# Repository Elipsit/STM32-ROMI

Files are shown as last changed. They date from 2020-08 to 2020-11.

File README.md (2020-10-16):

# STM32-ROMI

## Project Description

The Silicon Valley [HomeBrew Robotics Club](http://www.hbrobotics.org/) built an awesome [FPGA ROMI](https://github.com/hbrc-fpga-class) robot late 2019. I was inspired to build my own version using an STM32F4  while keeping the board compatable with the previous Polulu ROMI base. The purpose of this was to familiarize myself with the STM32 environment and get a cool robot out of it. 

The robot is designed to compete in the HBRC TableTop Challenge:

A challenge where robots succeed by staying on the table or paying the price.

Stage 1: Walk autonomously from one end of the table to the other without falling off.
Stage 2: Find and push a block off of the table.
Stage 3: Find and push a block off of the table into a box at the edge of the table.

### Project Status
Robot is operational - working on tuning the PID loop for smooth driving
 **This project is still a work in progress**

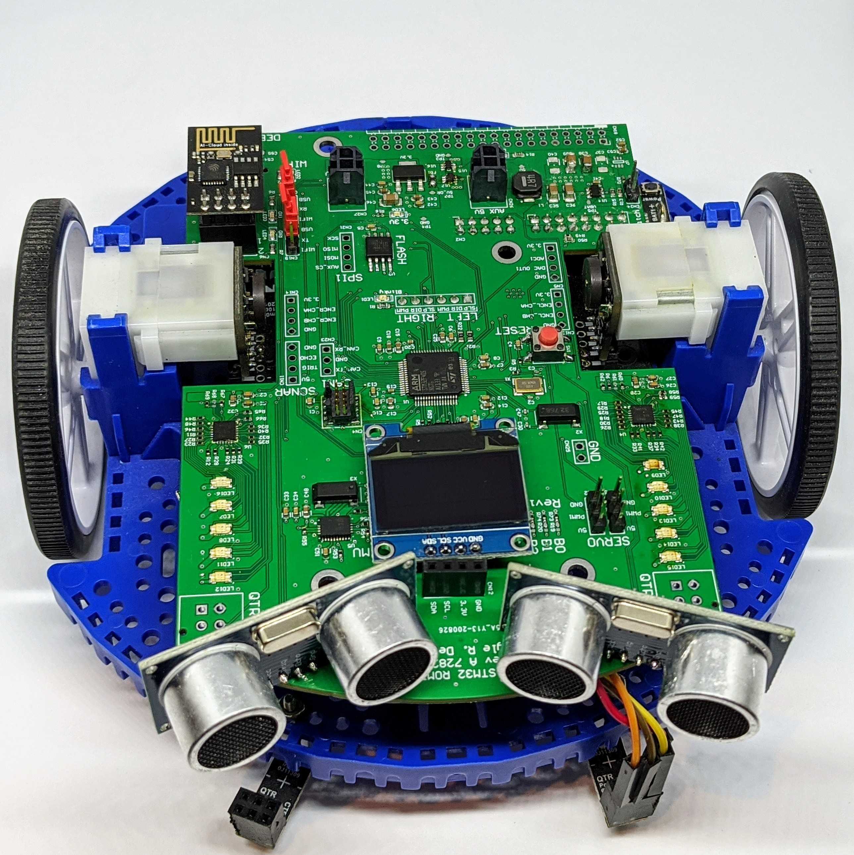
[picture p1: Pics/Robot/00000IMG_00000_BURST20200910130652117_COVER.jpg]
Robot_Front


## Design Files
### Electrical Design Files
This project was designed in Altium Designer 20

#### Datasheets
- [DRV8838 Motor Driver](https://www.ti.com/lit/ds/symlink/drv8838.pdf?HQS=TI-null-null-digikeymode-df-pf-null-wwe&ts=1599069814852)

### Motor Driver

The DRV8838 offers a simple two-pin PHASE/ENABLE control interface, which this board makes available for each motor as DIR and PWM, respectively. The DIR pin determines the motor direction (low drives the motor forward, high drives it in reverse) and the PWM pin can be supplied with a PWM signal to control the motor speed. The DIR and PWM control inputs are pulled low through weak internal pull-down resistors (approximately 100 kΩ). When the PWM pin is low, the motor outputs are both shorted to ground, which results in dynamic braking of a connected motor.

The two drivers’ SLEEP pins (labeled SLP) are connected together by default and can be driven low to put the drivers into a low-power sleep mode and turn off the motor outputs, which is useful if you want to let the motors coast. The SLEEP pins are pulled high through 10 kΩ pull-up resistors on the board so that the drivers are awake by default. In most applications, these pins can be left disconnected; if you want independent control of SLEEP on each side, you can cut the jumper labeled SLP L = R. The two SLEEP pins should not be driven separately without cutting this jumper.

The following simplified truth table shows how each driver operates:

#### Motor Driver Truth Table
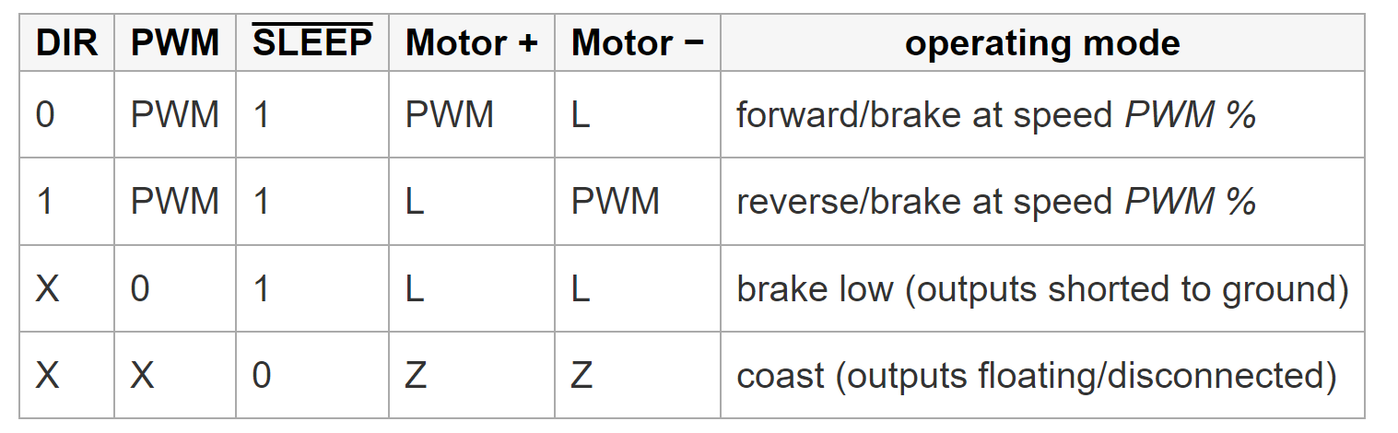
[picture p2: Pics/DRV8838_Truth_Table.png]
Truth Table


### PCBA
This project was manufactured by JLCPCB as an excuse for me to test their PCBA service.
*They didn't sponcer me I just wanted to try it out*

## Requited Parts

- [Romi Chassis Kit](https://www.pololu.com/product/3506)

- [Romi Encoder Pair Kit, 12 CPR, 3.5-18V](https://www.pololu.com/product/3542)

- [Motor Driver and Power Distribution Board for Romi Chassis](https://www.pololu.com/product/3543)

- [QTR-1A Reflectance Sensor (2-Pack)](https://www.pololu.com/product/2458)

- [0.96 Inch OLED](https://www.amazon.com/UCTRONICS-SSD1306-Self-Luminous-Display-Raspberry/dp/B072Q2X2LL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)

- [HC-SRO4](https://www.amazon.com/Smraza-Ultrasonic-Distance-Mounting-Duemilanove/dp/B01JG09DCK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)

### 3D Print Files
- [Sonar Servo Mount](https://www.thingiverse.com/thing:1423)

# Bring Up
The Uart2 channel can be connected to the CH340C; USB to serial converter, or an ESP8266 running [esp-link](https://github.com/jeelabs/esp-link) as a telnet connection

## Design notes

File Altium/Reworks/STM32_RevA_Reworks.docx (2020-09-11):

# STM32-ROMI Rev A Reworks

No table of contents entries found.

Date Modified | Revision | Author | Changes

# Wifi RX/TX

## Issue

Rx and Tx are flipped on ESP-01 moodule

## Solution

Cut trace and flywire

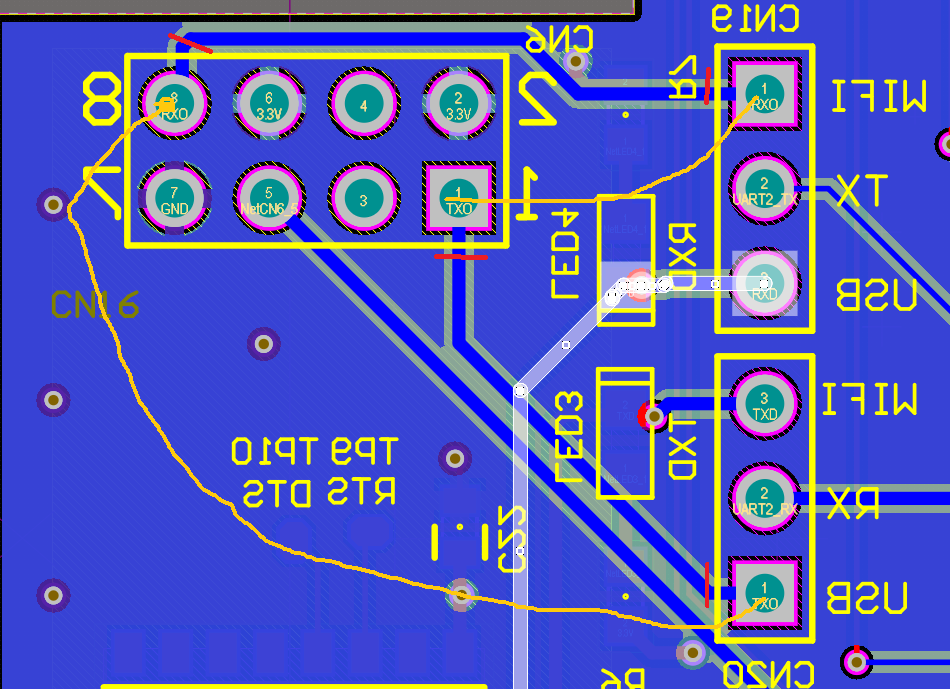
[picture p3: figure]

Cut the traces (cuts in red) at the base and fly wire correctly

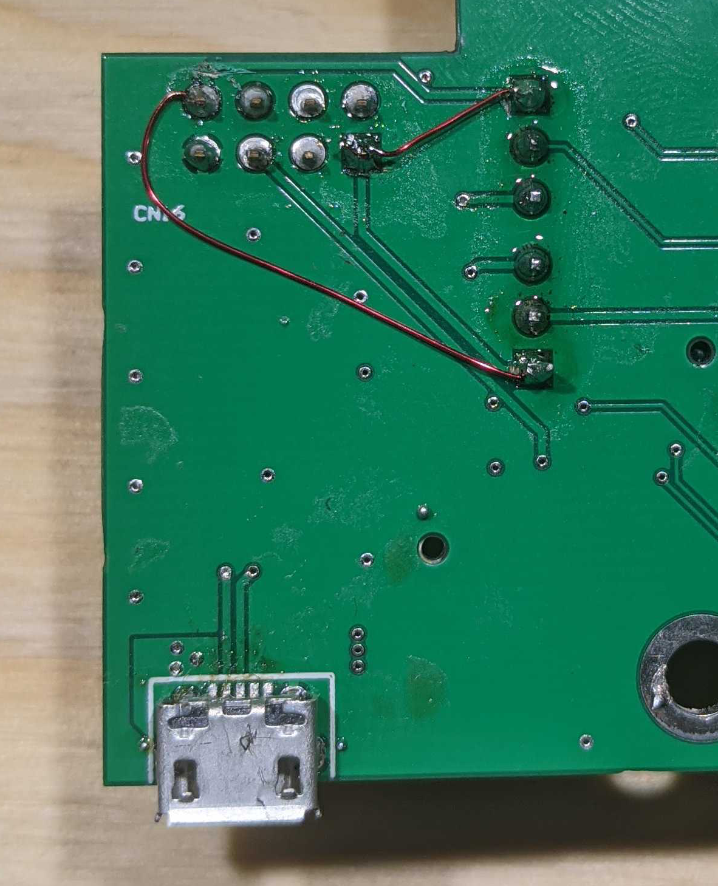
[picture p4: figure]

# PWMR

## Issue

Rx and Tx are flipped on ESP-01 moodule

## Solution

Cut trace and flywire

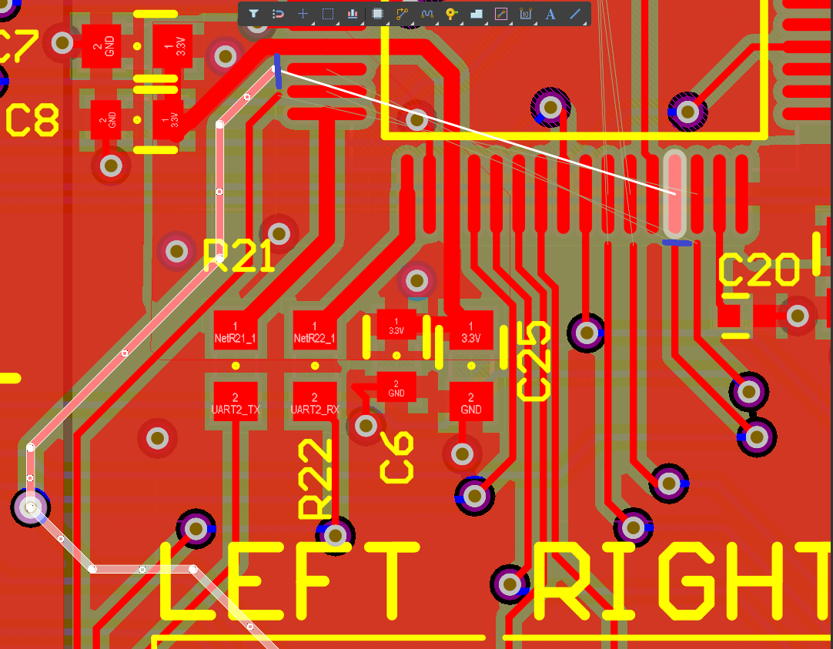
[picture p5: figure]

# PWMR

## Issue

Rx and Tx are flipped on ESP-01 moodule

## Solution

Cut trace and flywire

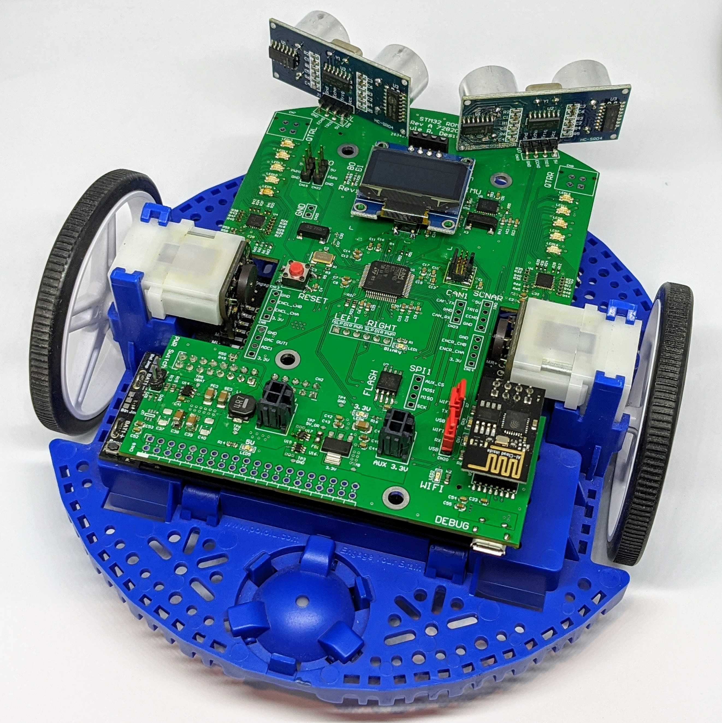
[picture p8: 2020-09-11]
Pics/Robot/00000IMG_00000_BURST20200910130628761_COVER.jpg

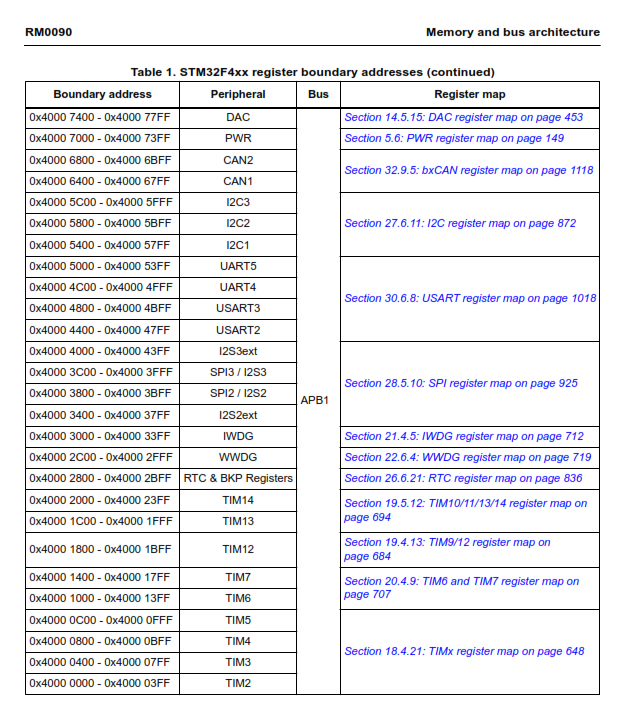
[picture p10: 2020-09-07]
Pics/Memory-2.png

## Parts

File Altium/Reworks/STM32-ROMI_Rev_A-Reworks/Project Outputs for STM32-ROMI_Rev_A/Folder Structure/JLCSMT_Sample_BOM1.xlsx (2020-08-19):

Comment | Designator | Footprint | LCSC Part #（optional）
100uF | C1 | CASE-B_3528 | C16133
100nF | C2, C9, C10 | 0603_C | C14663
10uF | C3-5 | 1206_C | C13585
15KΩ | R5, R6 | 0603_R | C22809

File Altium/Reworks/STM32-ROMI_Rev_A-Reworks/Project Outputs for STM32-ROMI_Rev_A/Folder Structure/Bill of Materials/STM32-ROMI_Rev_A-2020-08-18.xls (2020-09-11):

Item # | Designator | Description | Name | Quantity | Manufacturer 1 | Manufacturer Part Number 1 | Footprint | LibRef | Note
1 | R4, R51, R52, R64, R69, R71, R73, R74, R75 | 0.0 0402 | 0 | 9 | Panasonic | ERJ-2GE0R00X | RESC0402(1005)_L | RES 0.0 OHM JUMPER 1/10W 0402
2 | R21, R22 | 0 0603 | 0 0603 | 2 | Vishay Dale | CRCW06030000Z0EAHP | RESC0603(1608)_N | RES 0.0 OHM 1/4W JUMP 0603 SMD
3 | C6, C26, C29, C33 | 0.01uF 50V 0603 | 0.01uF | 4 | KEMET | C0603C103K5RACTU | CAPC0603(1608)_L | CAP CER 0.01uF 50V 10% X7R 0603
4 | C1, C4, C5, C8, C9, C10, C11, C12, C13, C24, C27, C31, C34, C51 | 0.1uF 0603 16V | 0.1uF | 14 | KEMET | C0603C104K4RACTU | CAPC0603(1608)_L | CAP CER 0.1UF 16V 10% X7R 0603
5 | C21, C22, C23, C41, C42, C44, C52, C54 | 0.1uF 0603 16V | 0.1uF | 8 | KEMET | C0603C104K4RACTU | CAPC0603(1608)_L | CAP CER 0.1UF 16V 10% X7R 0603
6 | R27, R28, R29, R30, R39, R40, R41, R42, R47, R48 | 1K 0402 | 1K | 10 | Mepco Philips | RC0402FR-071KL | RESC0402(1005)_L | RES 1K OHM 1% 1/16W 0402
7 | R2, R6, R7, R14 | 1.0K 0603 | 1.0K | 4 | Stackpole Electronics | RMCF0603FT1K00 | RESC0603(1608)_N | RES 1K OHM 1% 1/10W 0603
8 | C7, C14, C15, C16, C17, C25, C28, C32, C43, C45, C48, C53, C55 | 1uF 0603 25V | 1uF | 13 | TDK | CGA3E1X7R1E105K080AC | CAPC0603(1608)_N | CAP CER 1UF 25V 10% X7R 0603
9 | C19, C20 | 2.2uF 0402 | 2.2uF | 2 | TDK | C1005X5R1V225K050BC | CAPC0402(1005)_L | CAP CER 2.2UF 35V 10% X5R 0402
10 | L1 | Power Inductors 3.3uH ±20% 5.5A SMD,5.2x4.7x3mm RoHS | 3.3uH 5.5A | 1 |  |  | YSPI0530-3R3M | FIXED IND 3.3UH 5.5A 28 MOHM SMD
11 | U16 | 3.3 volt fixed regulator, 800mA | 3.3V | 1 | STMicroelectronics | LD1117S33TR | DSO-G3 | LD1117S33
12 | LED6 | LED GREEN CLEAR THIN 0603 SMD | 3.3V | 1 | Vishay Lite-On | LTST-C191KGKT | SM-LED-0603 | LTST-C191KGKT
13 | R56, R57, R58, R59, R60, R65, R66, R67 | 4.7K 0402 | 4.7K | 8 | Yageo | RC0402FR-074K7L | RESC0402(1005)_N | RES 4.7K OHM 1% 1/10W 0402
14 | LED5 | LED GREEN CLEAR THIN 0603 SMD | 5V | 1 | Vishay Lite-On | LTST-C191KGKT | SM-LED-0603 | LTST-C191KGKT
15 | X1 | 8Mhz ABM3 Parallel Load Crystal | 8Mhz | 1 | Abracon | ABM3B-8.000MHZ-B2-T | SMXOSC/5x3.2 | CRYSTAL 8MHZ ABM3
16 | R53, R54, R55, R62 | 10K 0402 | 10K | 4 | Samsung | RC1005F103CS | RESC0402(1005)_N | RES 10K OHM 1% 1/16W 0402
17 | R8, R9, R10, R15, R50 | 10K 0603 | 10K 1% | 5 | Panasonic | ERJ-3EKF1002V | RESC0603(1608)_L | RES 10K OHM 1/10W 1% 0603 SMD
18 | C35, C36, C37, C38, C39, C40, C46 |  | 10uF | 7 | Murata | GCM31CR71C106KA64L | CAPC1206(3216)_M | CAP CER 10UF 16V 1206
19 | C18 | 10uF 0603 10V | 10uF | 1 | Taiyo Yuden | LMK107BBJ106MAHT | CAPC0603(1608)_L | CAP CER 10UF 10V 20% X5R 0603
20 | C2, C3, C30, C47, C49, C50 | 20pF 0402 | 20pF 0402 | 6 | Murata | GRM1555C1H200GA01D | CAPC0402(1005)_L | CAP CER 20PF 50V 2% NP0 0402
21 | X2, X3 | SMD CRYSTAL RESONATORS 32.768KHZ ±20PPM SMD-3215_2P ROHS | 32.768 XO | 2 | Abracon | ABS25-32.768KHZ-6-T | OSCABS | DST310S 32.768KHz
22 | R13 | RES SMD 56.2K OHM 1% 1/10W 0603 | 56.2K | 1 | Panasonic | ERJ-3EKF5622V | RESC0603(1608)_L | RES SMD 56.2K OHM 1% 1/10W 0603
23 | R16 | 100 0402 | 100 | 1 | Yageo | RC0402FR-07100RL | RESC0402(1005)_N | RES 100 OHM 1% 1/16W 0402
24 | R5, R49, R70 | 100K 0402 | 100K 0402 | 3 | SEI | RMCF0402FT100K | RESC0402(1005)_L | RES 100K OHM 1% 1/16W 0402
25 | R3 | 220 0402 | 220 | 1 | Panasonic | ERJ-2RKF2200X | RESC0402(1005)_L | RES 220 OHM 1% 1/10W 0402
26 | R1 | 576OHMS ±1% 1/10W 0603 | 576 | 1 |  |  | RESC0603(1608)_N | 576
27 | FB1 | 600 OHM 0805 2.0A | 600 Ohm @ 100MHz | 1 | Wurth Electronics | 742792040 | RESC0805(2012)_N | FERRITE 600 OHM 2.0A 0805
28 | R11, R12, R17, R18, R23, R24, R25, R26, R31, R32, R33, R34, R35, R36, R37, R38, R43, R44, R45, R46 | 604 0402 | 604 | 20 | Panasonic | ERA-2AEB6040X | RESC0402(1005)_L | RES 604 OHM 1% 1/10W 0402
29 | CN27 | Molex Microfit 1x2 Vert Header | AUX 3.3V | 1 | Molex | 430450227 | Molex 1x2 Microfit 3.0 | MICROFIT 3.0 HDR VERT CPI 2CKT
30 | CN26 | Molex Microfit 1x2 Vert Header | AUX 5V | 1 | Molex | 430450227 | Molex 1x2 Microfit 3.0 | MICROFIT 3.0 HDR VERT CPI 2CKT
31 | LED1 | LED GREEN CLEAR THIN 0603 SMD | Blinky | 1 | Vishay Lite-On | LTST-C191KGKT | SM-LED-0603 | LTST-C191KGKT
32 | U5 | 9-Axis Intertial Sensor | BNO055 | 1 |  |  | LGA-28-3.8x5.2mm | CMP-010-0024-02
33 | CN23 | Header, 3-Pin | CAN1 | 1 | Sullins | PRPC003SAAN-RC | HDR1X3 | Header 3
34 | U3 | USB to Serial UART | CH340C | 1 |  |  | SOP-16 | CH340C
35 | CN6 | Header, 4-Pin, Dual row | CN/ESP-01 | 1 |  |  | ESP-01 | CN/ESP-01
36 | LED7, LED8, LED9, LED10, LED11, LED12, LED13, LED14, LED15, LED16 | RGB 620NMRED, 520NMGREEN, 465NMBLUE SMD, | E6C1206RGBC3UDA | 10 |  |  | E6C1206RGBC3UDA | RGB LED
37 | CN25 | Header, 2-Pin | GND | 1 | Sullins | PRPC002SAAN-RC | HDR1X2 | Header 2
38 | CN15, CN22 | Header, 3-Pin | Header 3 | 2 | Sullins | PRPC003SAAN-RC | HDR1X3 | Header 3
39 | CN5, CN9, CN10, CN11, CN12, CN13, CN14, CN21 | Header, 4-Pin | Header 4 | 8 | Sullins | PRPC004SAAN-RC | HDR1X4 | Header 4
40 | CN1 | Header, 6-Pin | Header 6 | 1 | Sullins | PRPC006SAAN-RC | PinHeader_1x06_P2.54mm_Vertical | Romi_Header 6
41 | CN18 | Header, 20-Pin, Dual row | Header 20X2 | 1 | Harwin | M20-9762046 | Raspberry_Pi_2_3 | J/Header 20X2
42 | U7, U15, U17 | OR Controller P-Channel 1.5A CC | Ideal Diode | 3 | Texas Instruments | LM66100DCKT | SC-70-6 | LM66100DCKT
43 | CN4 | SAMTEC - FTSH-105-01-L-DV - HEADER, 1.27MM, SMD, 10WAY | JTAG | 1 | Samtec | FTSH-105-01-L-DV | BOBS FAVORITE DEBUG HDR | CONN-2x5-SWD
44 | CN16 | Amphenol FCI CONN USB MICRO B RECPT SMT R/A | MicroUSB | 1 | Amphenol ICC / FCI | 10118194-0001LF | 10118194-0001LF | 10118194-0001LF
45 | U2 | 16M NOR Flash | MX25L1606E | 1 | Macronix | MX25L1606EM2I-12G | SOG.050/8D | MX25L1606E
46 | CN17 | SSD1306 I2C OLED 0.96" | OLED 0.96" | 1 |  |  | OLED_0.96_I2C | OLED_0.96_I2C
47 | CN24 | Header, 2-Pin | PWR Switch | 1 | Sullins | PRPC002SAAN-RC | HDR1X2 | Header 2
48 | CN7 | Molex Microfit 2x2 Vert Header | QTR_LEFT | 1 | Molex | 430450427 | Molex 2x2 Microfit | MICROFIT 3.0 HDR VERT 4CKT
49 | CN8 | Molex Microfit 2x2 Vert Header | QTR_RIGHT | 1 | Molex | 430450427 | Molex 2x2 Microfit | MICROFIT 3.0 HDR VERT 4CKT
50 | SW1, SW2 | SWITCH TACTILE SPST-NO 0.05A 12V | RESET | 2 | ITT C&K | PTS645SK50SMTR92LFS | SW TACT Red 6mm x 6mm | SW-PB SMD 5mm Red
51 | CN3 | Header, 8-Pin, Dual row | Romi_Header 8X2 | 1 |  |  | PinHeader_2x08_P2.54mm_Vertical | Romi_Header 8X2
52 | CN2 | Header, 5-Pin, Dual row | Romi-Header 5X2 | 1 |  |  | PinHeader_2x05_P2.54mm_Vertical - duplicate | Romi-Header 5X2
53 | LED4 | LED GREEN CLEAR THIN 0603 SMD | RXD | 1 | Vishay Lite-On | LTST-C191KGKT | SM-LED-0603 | LTST-C191KGKT
54 | U1 | IC MCU 32BIT 1MB FLASH 64LQFP | STM32F405RGT6 | 1 | STMicroelectronics | STM32F405RGT6 | STM-LQFP64_N | STM32F405RGT6
55 | CN20 | Header, 3-Pin | STM_RX | 1 | Sullins | PRPC003SAAN-RC | HDR1X3 | Header 3
56 | CN19 | Header, 3-Pin | STM_TX | 1 | Sullins | PRPC003SAAN-RC | HDR1X3 | Header 3
57 | U4, U6 | IC I/O EXPANDER I2C SMBUS 24VQFN | TCA9555RGER | 2 | Texas Instruments | TCA9555RGER | QFN50P400X400X100_HS-25N | CMP-001-0784-04
58 | U14 | IC REG BUCK ADJ 3A TSOT23-6 | TPS563209DDCR | 1 | Texas Instruments | TPS563209DDCR | SOT23-6 | TPS563209DDCR
59 | LED3 | LED GREEN CLEAR THIN 0603 SMD | TXD | 1 | Vishay Lite-On | LTST-C191KGKT | SM-LED-0603 | LTST-C191KGKT
60 | LED2 | LED GREEN CLEAR THIN 0603 SMD | WIFI | 1 | Vishay Lite-On | LTST-C191KGKT | SM-LED-0603 | LTST-C191KGKT

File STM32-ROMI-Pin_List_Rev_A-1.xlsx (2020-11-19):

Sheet: Pin Map
Chip Line: | STM32F405RGT6 |  |  |  |  | STM32F405RGT6 | OLD
Pin Number | Pin Name | Net Class | Net Name | Connected Component | Old Pin | Pin Name | Net Class | Net Name | Connected Component
60 | BOOT0 |  |  |  |  | BOOT0
7 | NRST | Reset |  |  |  | NRST | Reset
14 | PA0 | Encoder | ENCL_CHA |  | PB10 | PA0 | PWM | PWMR | CN1
15 | PA1 | Encoder | ENCL_CHB |  | PB11 | PA1 | ADC | ADC_IN1
43 | PA10 | SONAR | TRIGR |  |  | PA10 | SONAR | TRIGR
44 | PA11 | CAN | CAN_RX |  |  | PA11 | CAN | CAN_RX
45 | PA12 | CAN | CAN_TX |  |  | PA12 | CAN | CAN_TX
46 | PA13 | SWO | SWDIO | PROGRAMMER |  | PA13 | SWO | SWDIO | PROGRAMMER
49 | PA14 | TCK | SWCLK | PROGRAMMER |  | PA14 | TCK | SWCLK | PROGRAMMER
50 | PA15 | SPI | SPI_CS_AUX |  |  | PA15 | SPI | SPI_CS_AUX
16 | PA2 | UART | UART2_TX |  |  | PA2 | UART | UART2_TX
17 | PA3 | UART | UART2_RX |  |  | PA3 | UART | UART2_RX
20 | PA4 | DAC | DAC_OUT1 |  |  | PA4 | DAC | DAC_OUT1
21 | PA5 | GPIO | BLINKY | LEDx |  | PA5 | GPIO | BLINKY | LEDx
22 | PA6 | SPI1 | SPI1_MISO |  |  | PA6 | SPI1 | SPI1_MISO
23 | PA7 | SPI1 | SPI1_MOSI |  |  | PA7 | SPI1 | SPI1_MOSI
41 | PA8 | I2C3 | I2C3_SCL |  |  | PA8 | I2C3 | I2C3_SCL
42 | PA9 | SONAR | ECHOR |  |  | PA9 | SONAR | ECHOR
26 | PB0 | SONAR | TRIGL |  |  | PB0 | Encoder | ENCR_CHA | CN14
27 | PB1 | SONAR | ECHOL |  |  | PB1 | Encoder | ENCR_CHB | CN15
29 | PB10 | PWM | PWMR | CN1 |  | PB10 | Encoder | ENCL_CHA | CN13
30 | PB11 | ADC |  |  |  | PB11 | Encoder | ENCL_CHB | CN14
33 | PB12 | QTR | QTRL_OUT |  |  | PB12 | QTR | QTRL_OUT
34 | PB13 | Motor CTRL | ROMI_DIRR |  |  | PB13 | Motor CTRL | ROMI_DIRR
35 | PB14 | Motor CTRL | ROMI_SLPR |  |  | PB14 | Motor CTRL | ROMI_SLPR
36 | PB15 | Servo | SERVO1_PWM |  |  | PB15 | Servo | SERVO1_PWM
28 | PB2 | QTR | QTRR_OUT |  |  | PB2 | QTR | QTRR_OUT
55 | PB3 | SPI1_SCK | SPI1_SCK |  |  | PB3 | SPI1_SCK | SPI1_SCK
56 | PB4 | Encoder | ENCR_CHA |  |  | PB4 | SONAR | TRIGL
57 | PB5 | Encoder | ENCR_CHB |  |  | PB5 | SONAR | ECHOL
58 | PB6 | PWM | ROMI_PWML | CN1 |  | PB6 | PWM | ROMI_PWML | CN1
59 | PB7 | I2C | I2C1_SDA |  |  | PB7 | I2C | I2C1_SDA
61 | PB8 | I2C | I2C1_SCL |  |  | PB8 | I2C | I2C1_SCL
62 | PB9 | Servo | SERVO2_PWM |  |  | PB9 | Servo | SERVO2_PWM
8 | PC0 | IMU | IMU_RST |  |  | PC0 | IMU | IMU_RST
9 | PC1 | Revision Bits | REV_BIT0 |  |  | PC1 | Revision Bits | REV_BIT0
51 | PC10 | UART RPI | UART4_TX |  |  | PC10 | UART RPI | UART4_TX
52 | PC11 | UART RPI | UART4_RX |  |  | PC11 | UART RPI | UART4_RX
53 | PC12 | Motor CTRL | ROMI_DIRL |  |  | PC12 | Motor CTRL | ROMI_DIRL
2 | PC13 | GPIO | OLED_BTN | Push Button |  | PC13 | GPIO | OLED_BTN | Push Button
3 | PC14 | RCC | RCC_OSC32_IN |  |  | PC14 | RCC | RCC_OSC32_IN
4 | PC15 | RCC | RCC_OSC32_OUT |  |  | PC15 | RCC | RCC_OSC32_OUT
10 | PC2 | Revision Bits | REV_BIT1 |  |  | PC2 | Revision Bits | REV_BIT1
11 | PC3 | Revision Bits | REV_BIT2 |  |  | PC3 | Revision Bits | REV_BIT2
24 | PC4 | RGB | RGB_INT1 |  |  | PC4 | RGB | RGB_INT1
25 | PC5 | RGB | RGB_INT2 |  |  | PC5 | RGB | RGB_INT2
37 | PC6 | Motor CTRL | ROMI_SLPL |  |  | PC6 | Motor CTRL | ROMI_SLPL
38 | PC7 | SONAR | ECHO_CTR |  |  | PC7 | SONAR | ECHO_CTR
39 | PC8 | SONAR | TRIG_CTR |  |  | PC8 | SONAR | TRIG_CTR
40 | PC9 | I2C3 | I2C3_SDA |  |  | PC9 | I2C3 | I2C3_SDA
54 | PD2 | Flash CS | SPI_CS_FLASH |  |  | PD2 | Flash CS | SPI_CS_FLASH
5 | RCC_OSC_IN | RCC | RCC_OSC_IN |  |  | RCC_OSC_IN | RCC | RCC_OSC_IN
6 | RCC_OSC_OUT | RCC | RCC_OSC_OUT |  |  | RCC_OSC_OUT | RCC | RCC_OSC_OUT
1 | VBAT | 3.3V | VBAT | 3.3V |  | VBAT | 3.3V | VBAT | 3.3V
13 | VDD |  |  |  |  | VDD
19 | VDD |  |  |  |  | VDD
32 | VDD |  |  |  |  | VDD
48 | VDD | Power |  |  |  | VDD | Power
64 | VDD |  |  |  |  | VDD
12 | VSS |  |  |  |  | VSS
18 | VSS |  |  |  |  | VSS
31 | VSS |  |  |  |  | VSS
47 | VSS | GND |  |  |  | VSS | GND
63 | VSS |  |  |  |  | VSS

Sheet: Timer Map
 |  |  |  |  | OLD
Type | Name | Purpose | Net |  | Type | Name | Purpose | Net
RTC | RTC |  |  |  | RTC | RTC
Advanced-Control Timer | TIM1 |  |  |  | Advanced-Control Timer | TIM1
General Purpose Timer | TIM2 | PWM Motor | PWM Right |  | General Purpose Timer | TIM2 | Encoder | Encoder Left
General Purpose Timer | TIM3 | Encoder | Encoder Right |  | General Purpose Timer | TIM3 | Encoder | Encoder Right
General Purpose Timer | TIM4 | PWM Motor | PWM Left |  | General Purpose Timer | TIM4 | PWM Motor | PWM Left
General Purpose Timer | TIM5 | Encoder | Encoder Left |  | General Purpose Timer | TIM5 | PWM Motor | PWM Right
Basic Timer | TIM6 | Blinky |  |  | Basic Timer | TIM6 | Blinky
Basic Timer | TIM7 | Encoder Poll |  |  | Basic Timer | TIM7 | Encoder Poll
Advanced-Control Timer | TIM8 |  |  | Change to use for gpio interupt. Reset timer, send trigger and increment timer to count. | Advanced-Control Timer | TIM8
General Purpose Timer | TIM9 | Ultrasonic mSec |  |  | General Purpose Timer | TIM9 | Ultrasonic mSec
General Purpose Timer | TIM10 |  |  |  | General Purpose Timer | TIM10
General Purpose Timer | TIM11 | Servo | Servo2 PWM |  | General Purpose Timer | TIM11 | Servo | Servo2 PWM
General Purpose Timer | TIM12 | Servo | Servo1 PWM |  | General Purpose Timer | TIM12 | Servo | Servo1 PWM
General Purpose Timer | TIM13 |  |  |  | General Purpose Timer | TIM13
General Purpose Timer | TIM14 |  |  |  | General Purpose Timer | TIM14

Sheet: Math
Sample Rate | 50 | HZ
Sample Period | 0.02 | Sec
Encoder Resolution | 12
Gear Ratio | 100 | to 1
Counts/rev | 1200
Wheel Diameter | 72 | mm
Wheel Circumference | 226.188 | mm
Counts/mm | 5.305321237
MAX RPM | 130 | rpm
Max RPS | 2.166666667 | rps
Max Rad/s | 13.60666667
Max Counts/Sec | 2600
Max Counts per sample | 52 | 1/sec
Counts/rad | 190.9915645
Enc to Rad/s | 0.2616666667
Enc/Vel
Rad/s

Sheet: Timer Calculator
Timer 2 | Motor Left
APB1 Timer Clock | Prescaler | Period | Frequency (HZ) | Interupt (Sec)
50000000 | 3 | 999 | 16683.35002 | 5.994e-05
Timer 4 | Motor Right
APB1 Timer Clock | Prescaler | Period | Frequency (HZ) | Interupt (Sec)
50000000 | 2 | 1000 | 25000 | 4e-05

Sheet: ROMI Connectors
Name | X | Y | Rotation | Layer
CN1 | 1939.5mil | 1879mil | 90 | Bottom
CN2 | 1939.5mil | 1086.1mil | 0 | Top
CN3 | 1339.5mil | 1086.1mil | 270 | Bottom

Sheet: Libraries
Neopixel | https://github.com/hubmartin/WS2812B_STM32F4
Possible LED Driver | https://lcsc.com/product-detail/LED-Drivers_MBI5020GP_C82600.html
clone of this | https://lcsc.com/product-detail/_STMicroelectronics_STP16CPC26MTR_STP16CPC26MTR_C157439.html
possible speaker | https://lcsc.com/product-detail/Audio-Power-OpAmps_AWINIC-Shanghai-Awinic-Tech-AW8736FCR_C252442.html

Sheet: I2C Map
Address | Component

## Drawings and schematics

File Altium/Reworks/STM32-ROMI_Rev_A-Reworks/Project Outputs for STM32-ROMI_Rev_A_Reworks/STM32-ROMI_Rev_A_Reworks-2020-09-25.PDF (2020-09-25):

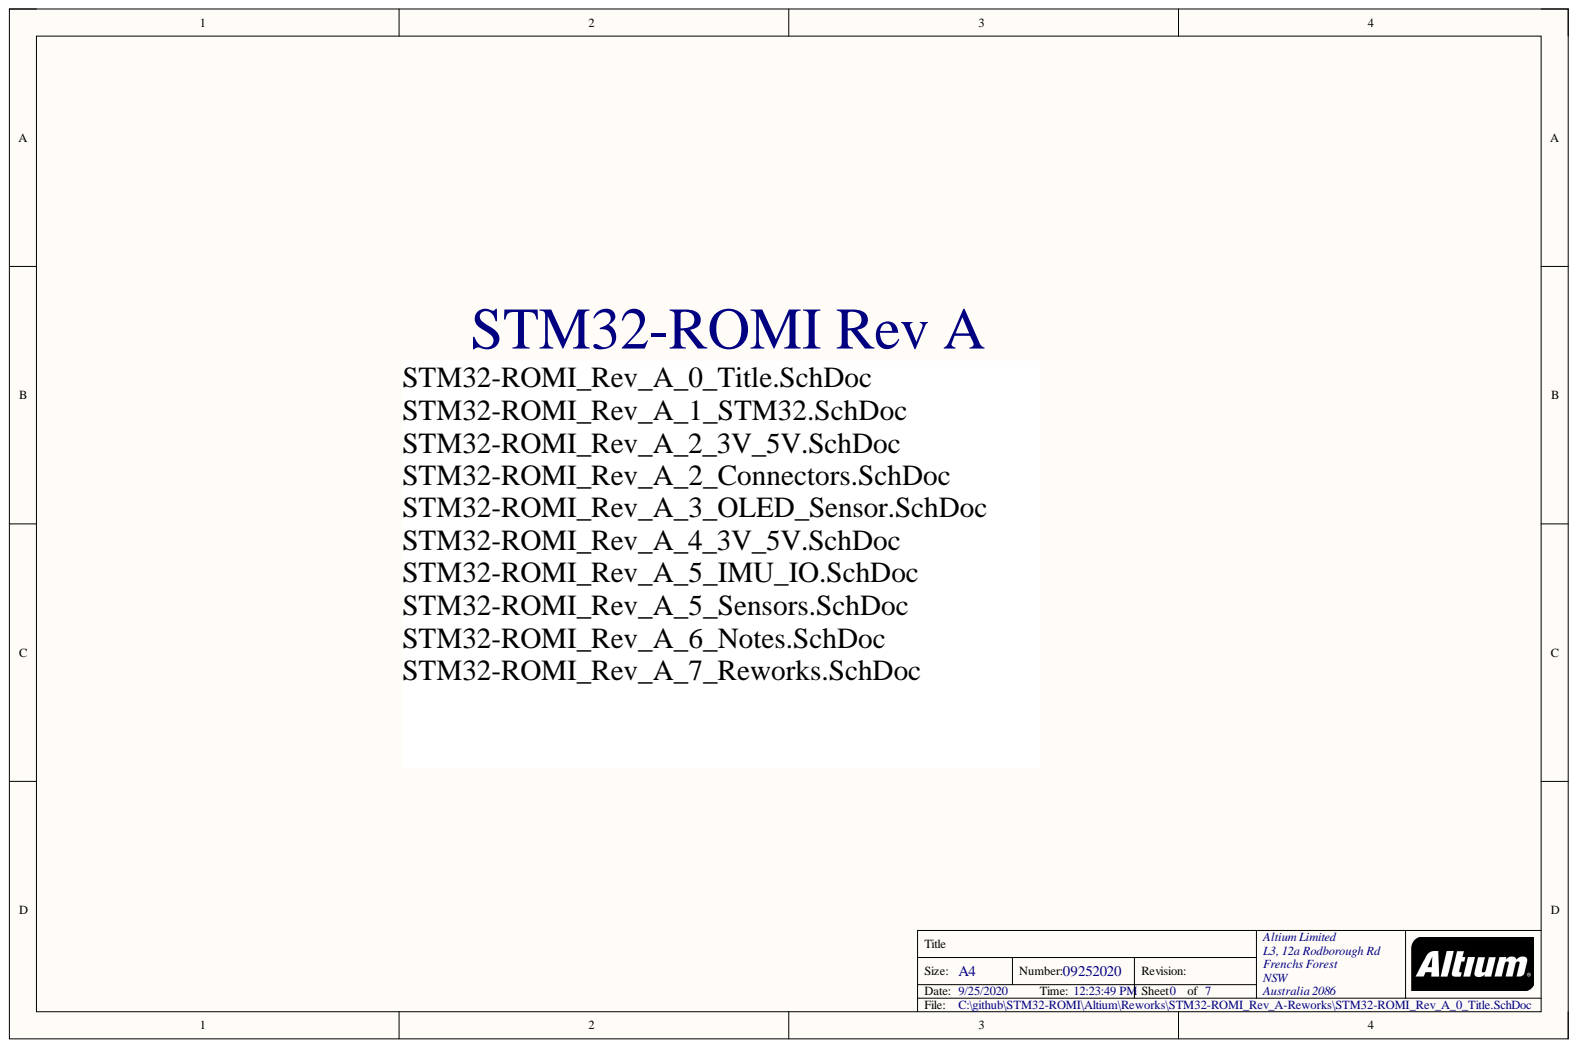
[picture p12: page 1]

Title | Altium Limited L3, 12a Rodborough Rd Frenchs Forest NSW Australia 2086

A4 Size: | 09252020 Number: | Revision:

Date: 9/25/2020 Time: 12:23:49 PM | | Sheet 0 of 7

C:\github\STM32-ROMI\Altium\Reworks\STM32-ROMI_Rev_A-Reworks\STM32-ROMI_Rev_A_0_Title.SchDoc

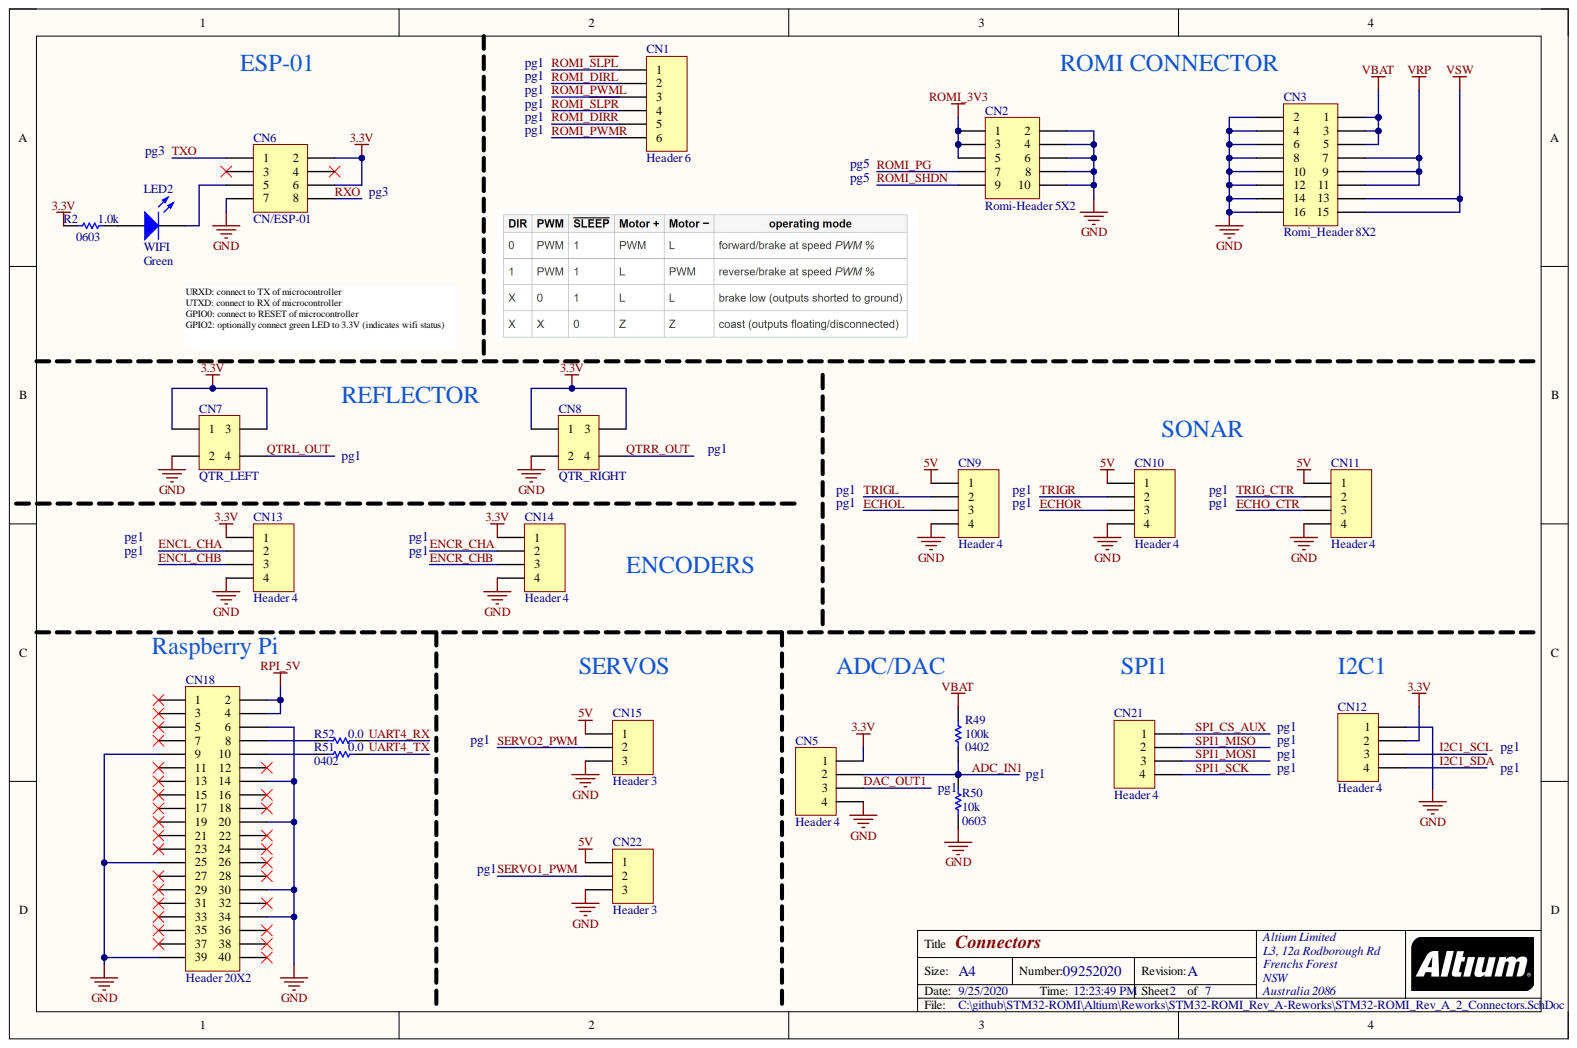
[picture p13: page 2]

URXD: connect to TX of microcontroller
UTXD: connect to RX of microcontroller
GPIO0: connect to RESET of microcontroller
GPIO2: optionally connect green LED to 3.3V (indicates wifi status)

Connectors Title | Altium Limited L3, 12a Rodborough Rd Frenchs Forest NSW Australia 2086

A4 Size: | 09252020 Number: | A Revision:

Date: 9/25/2020 Time: 12:23:49 PM | | Sheet 2 of 7

C:\github\STM32-ROMI\Altium\Reworks\STM32-ROMI_Rev_A-Reworks\STM32-ROMI_Rev_A_2_Connectors.SchDoc

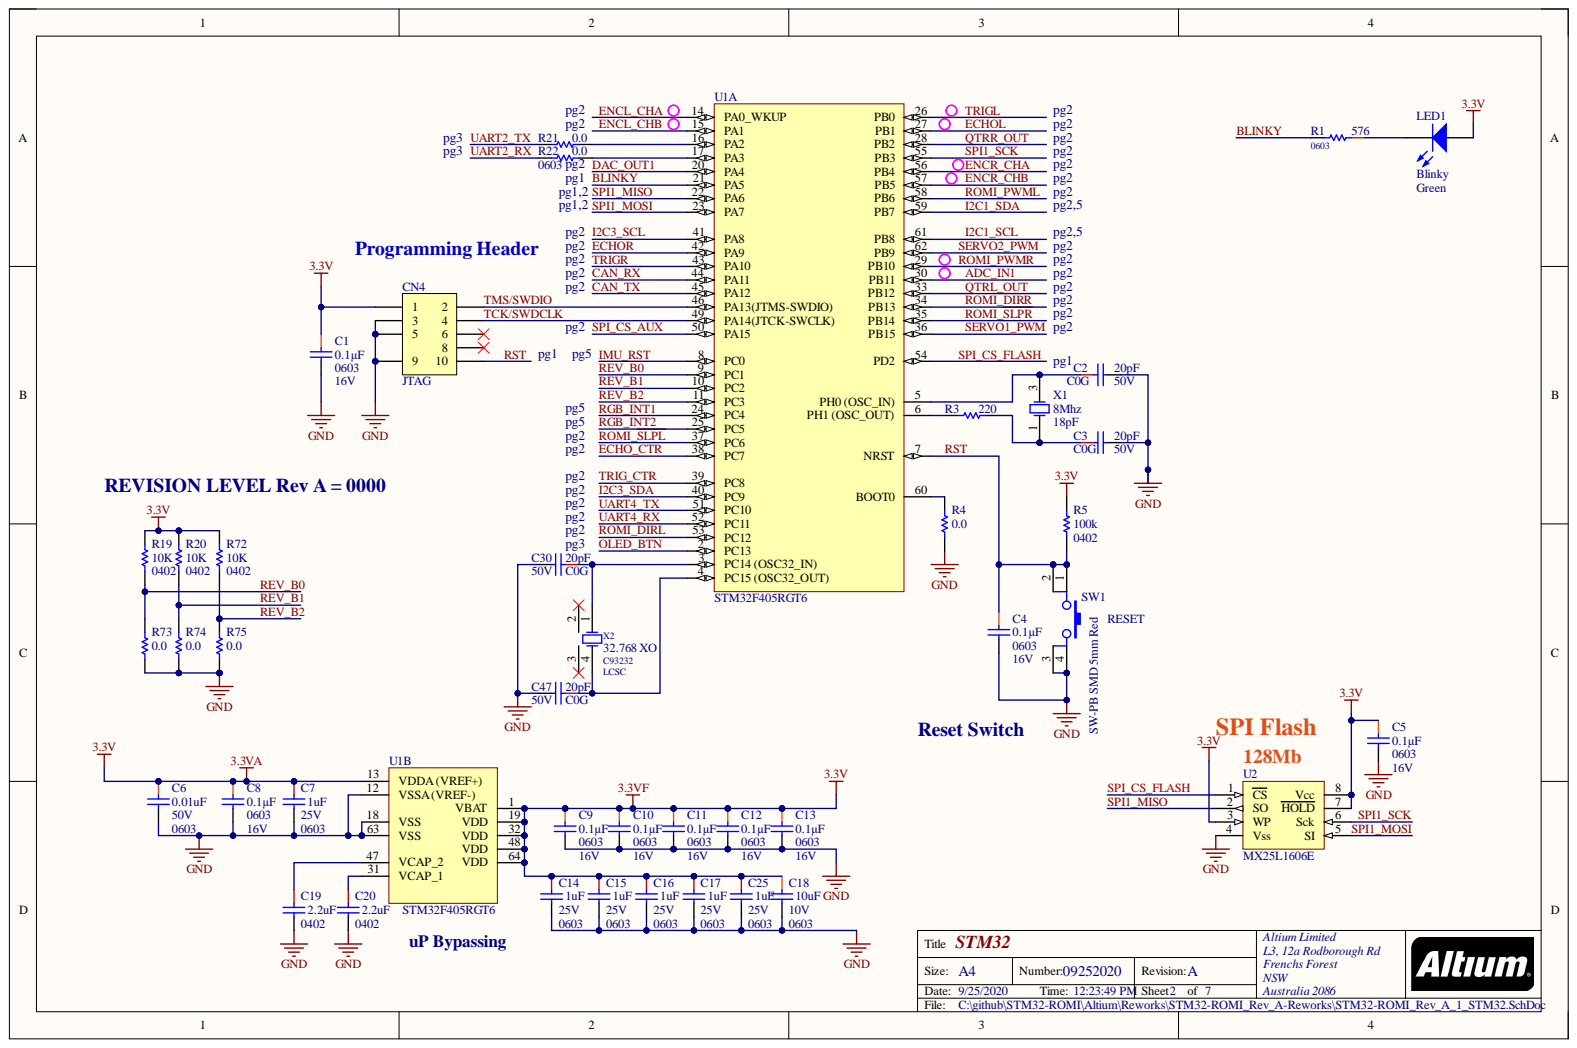
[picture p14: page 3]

TCK/SWDCLK | PA14(JTCK-SWCLK) 49 | ROMI_SLPR

SPI_CS_AUX pg5 pg2 pg2 pg2 pg2 pg2 | PA15 50 | SERVO1_PWM

0.0 | | REV_B1

0.0 | REV_B2

C:\github\STM32-ROMI\Altium\Reworks\STM32-ROMI_Rev_A-Reworks\STM32-ROMI_Rev_A_1_STM32.SchDoc

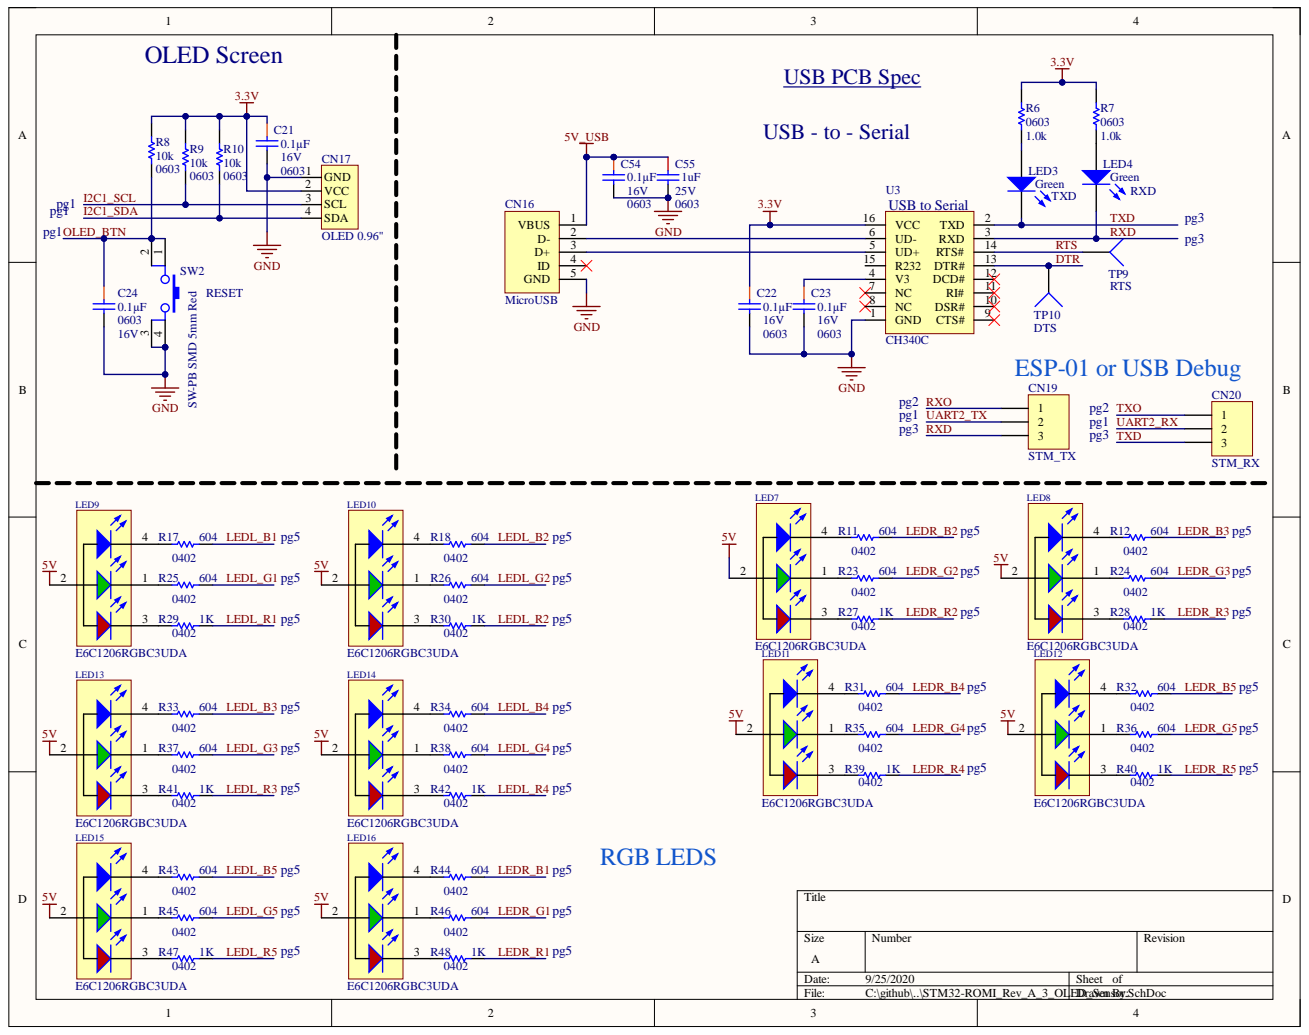
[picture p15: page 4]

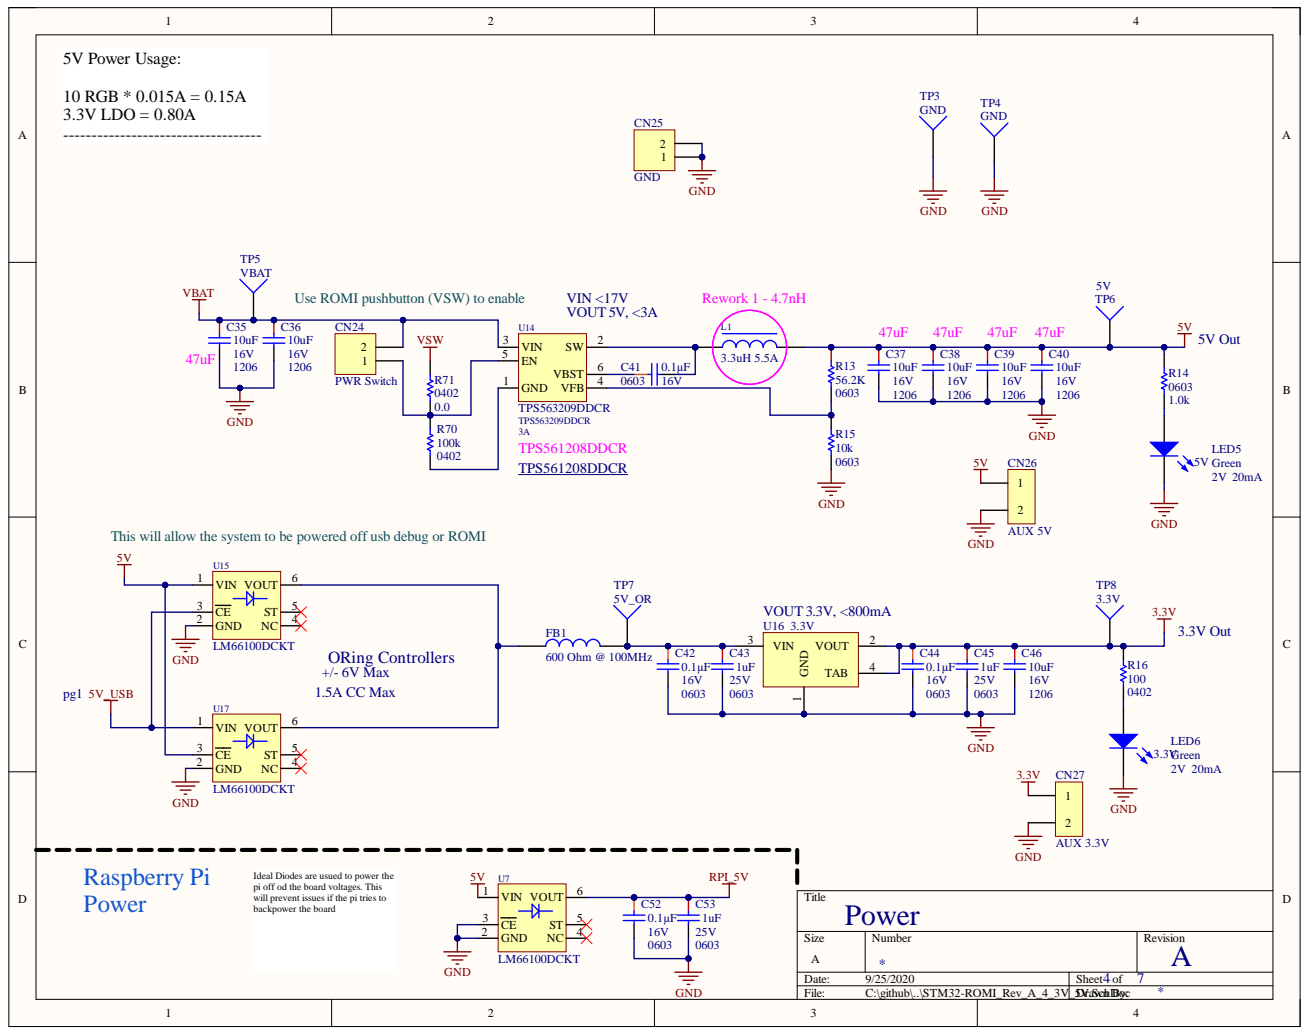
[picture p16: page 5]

Use ROMI pushbutton (VSW) to enable

This will allow the system to be powered off usb debug or ROMI

Ideal Diodes are usued to power the
pi off od the board voltages. This
will prevent issues if the pi tries to
backpower the board

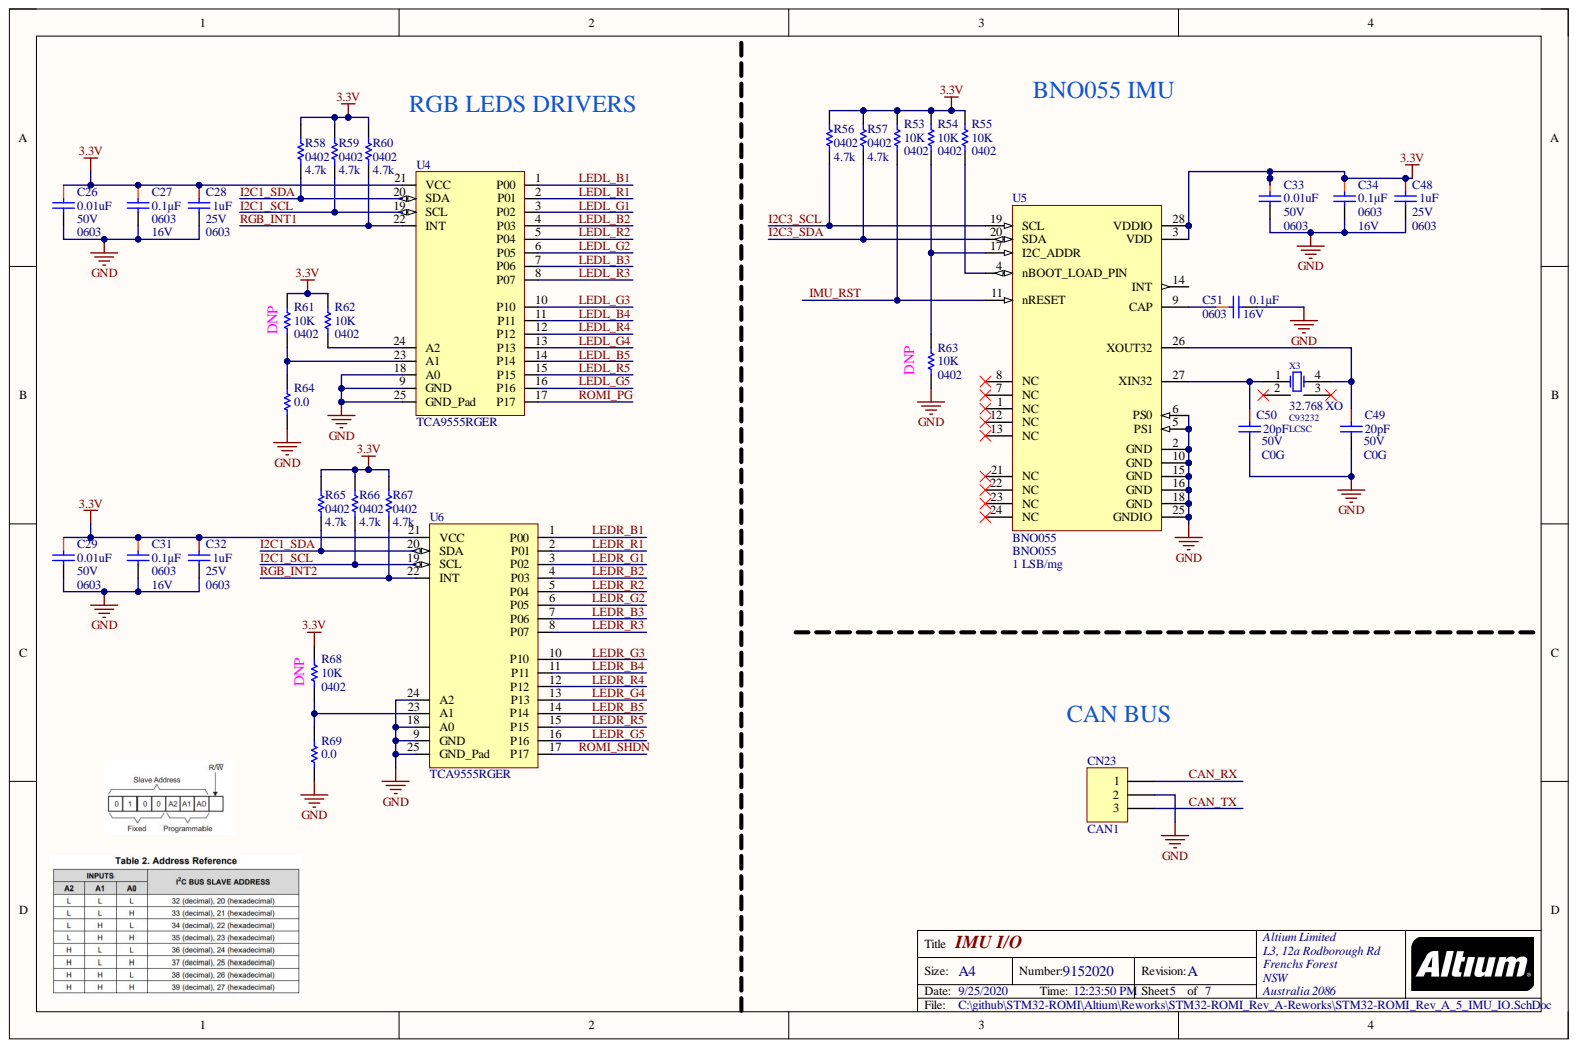
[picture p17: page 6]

IMU I/O Titl e | Altium L i mite d L3, 12a Rodborough Rd Frenchs Forest NSW Austral ia 20 86

A4 S i z e : | 9 1 5 2 0 2 0 Numbe r : | A R e vision:

Date : 9/25/202 0 Time : 12:23:50 P M | | She e t 5 of 7

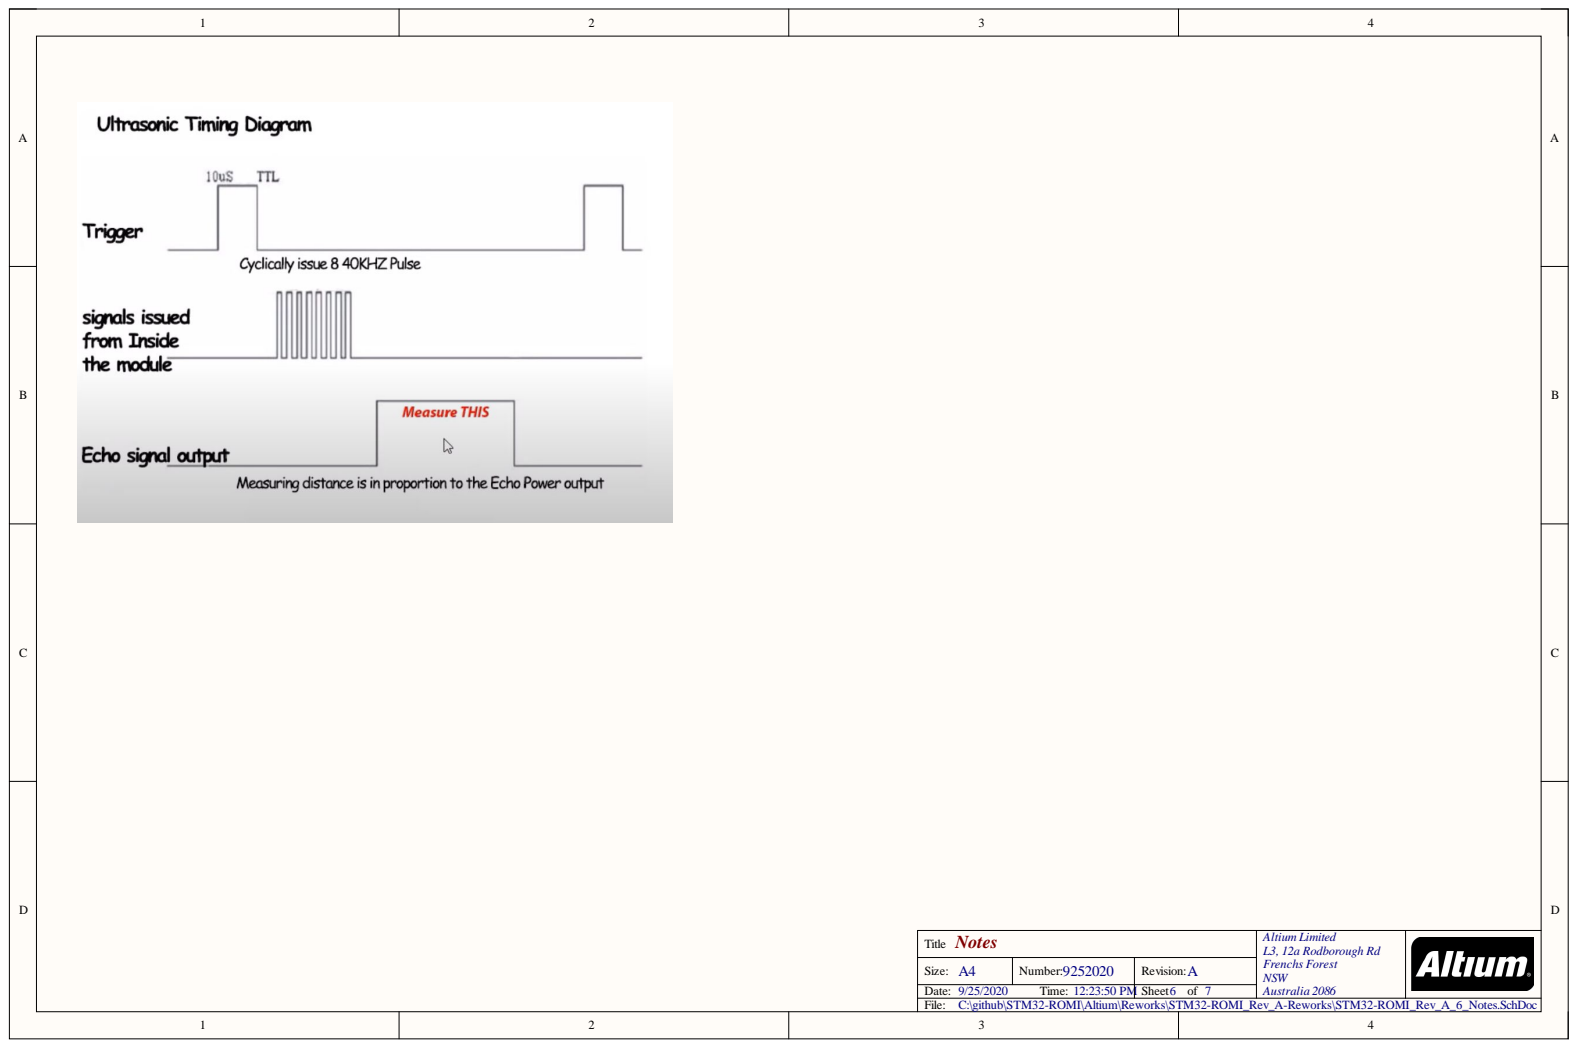
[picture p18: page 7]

Notes Title | Altium Limited L3, 12a Rodborough Rd Frenchs Forest NSW Australia 2086

A4 Size: | 9252020 Number: | A Revision:

Date: 9/25/2020 Time: 12:23:50 PM | | Sheet 6 of 7

C:\github\STM32-ROMI\Altium\Reworks\STM32-ROMI_Rev_A-Reworks\STM32-ROMI_Rev_A_6_Notes.SchDoc

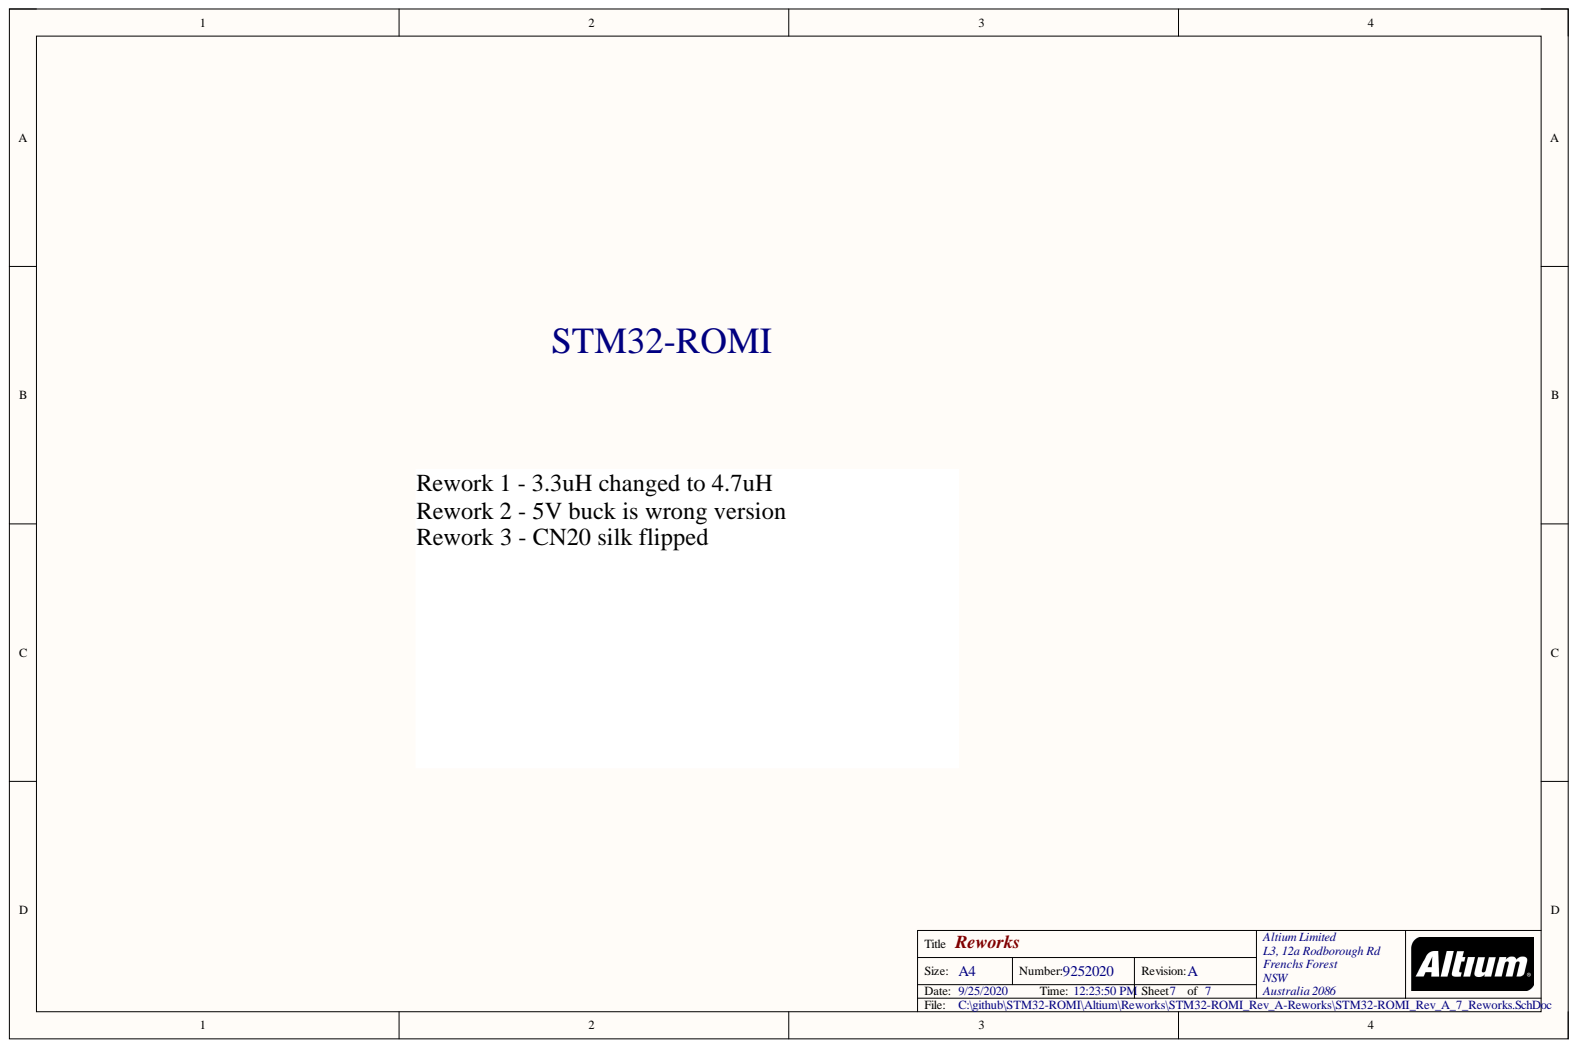
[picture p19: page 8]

Rework 1 - 3.3uH changed to 4.7uH
Rework 2 - 5V buck is wrong version
Rework 3 - CN20 silk flipped

Reworks Title | Altium Limited L3, 12a Rodborough Rd Frenchs Forest NSW Australia 2086

A4 Size: | 9252020 Number: | A Revision:

Date: 9/25/2020 Time: 12:23:50 PM | | Sheet 7 of 7

C:\github\STM32-ROMI\Altium\Reworks\STM32-ROMI_Rev_A-Reworks\STM32-ROMI_Rev_A_7_Reworks.SchDoc

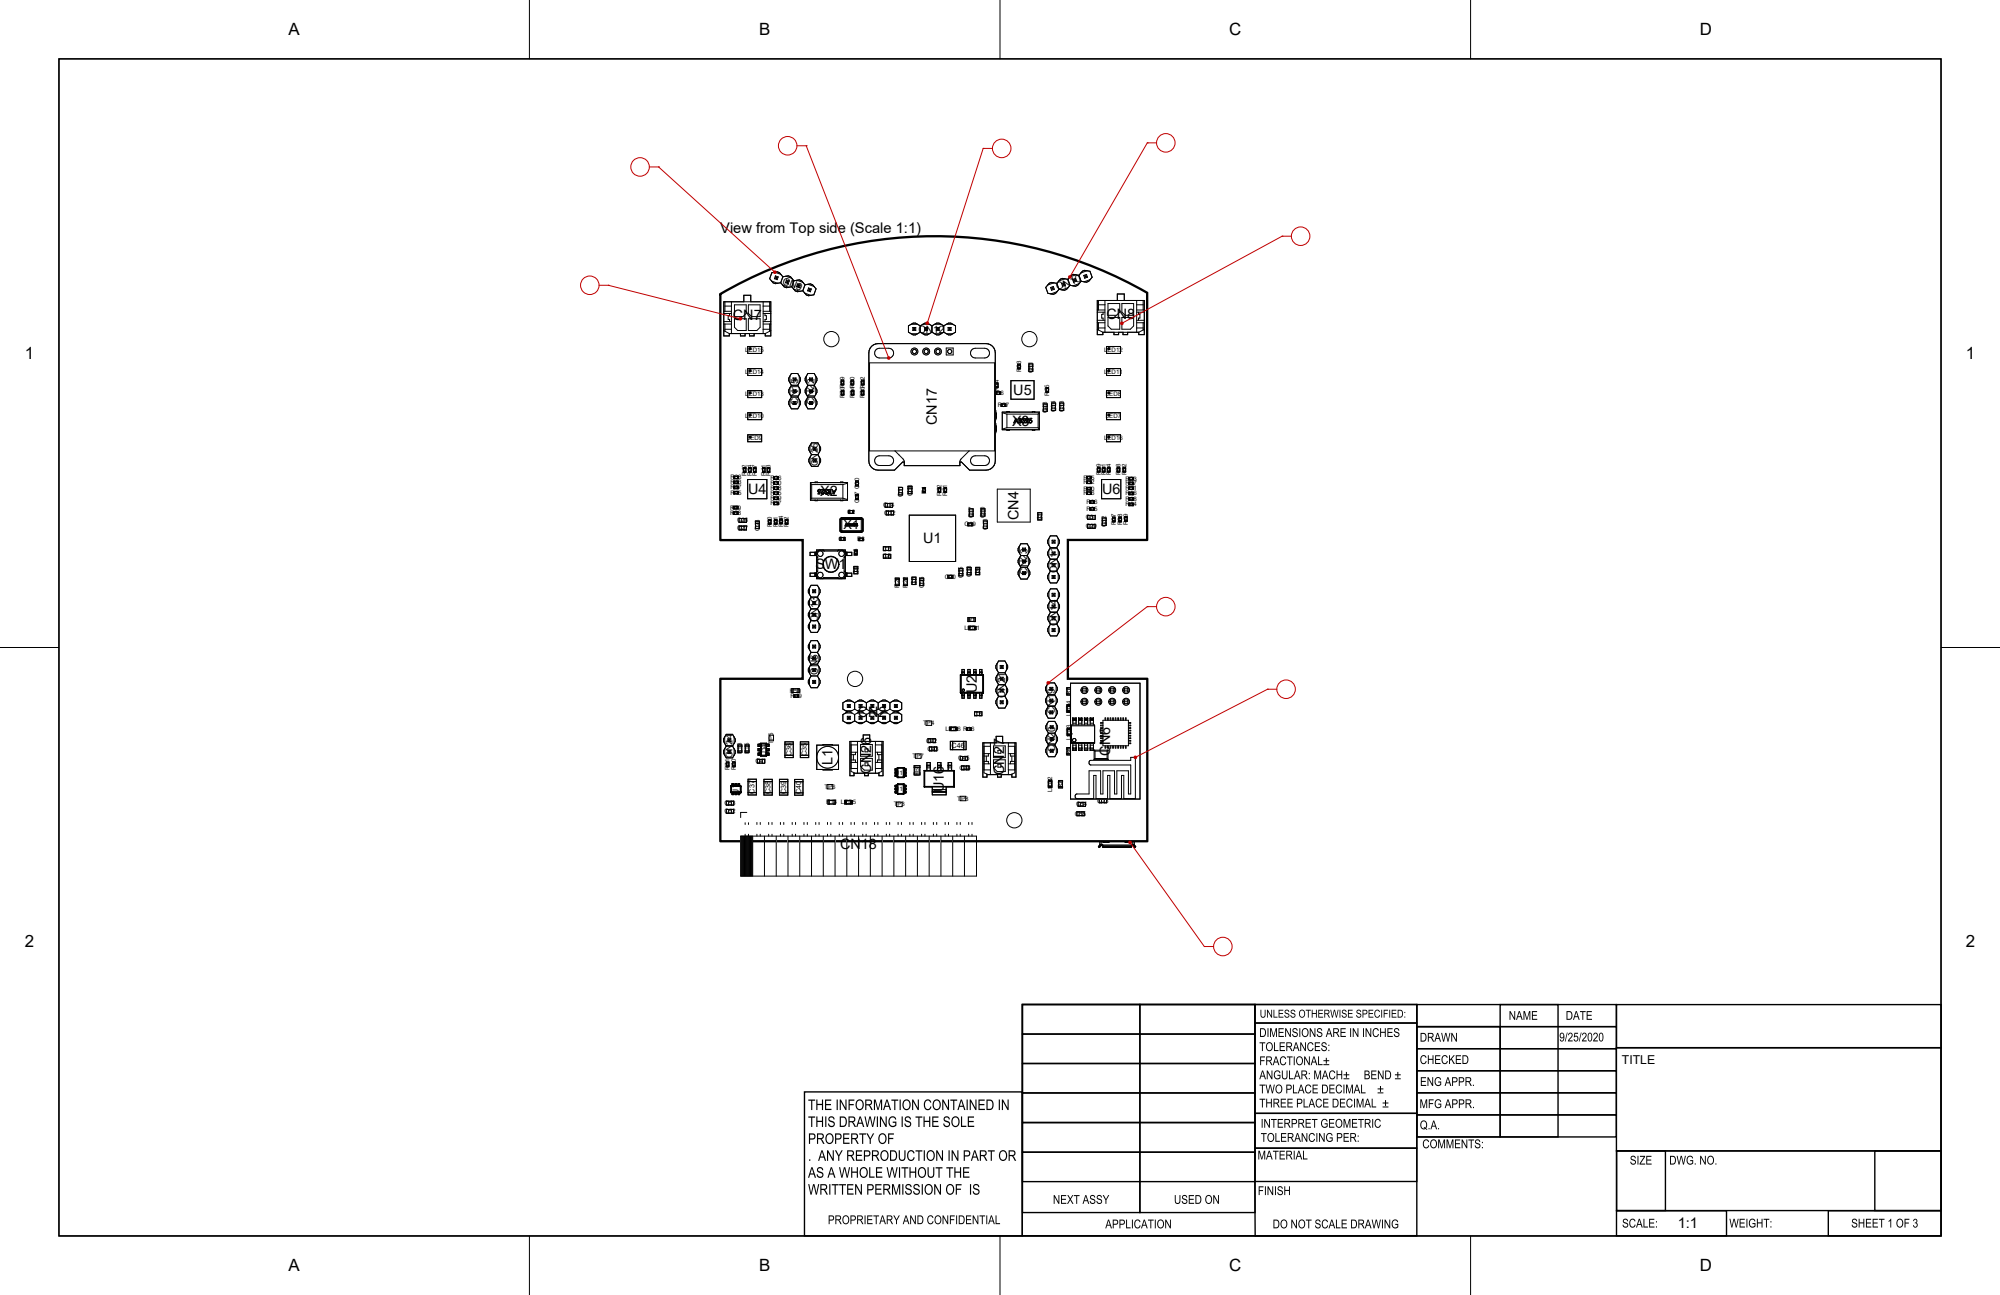
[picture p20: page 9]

View from Top side (Scale 1:1)

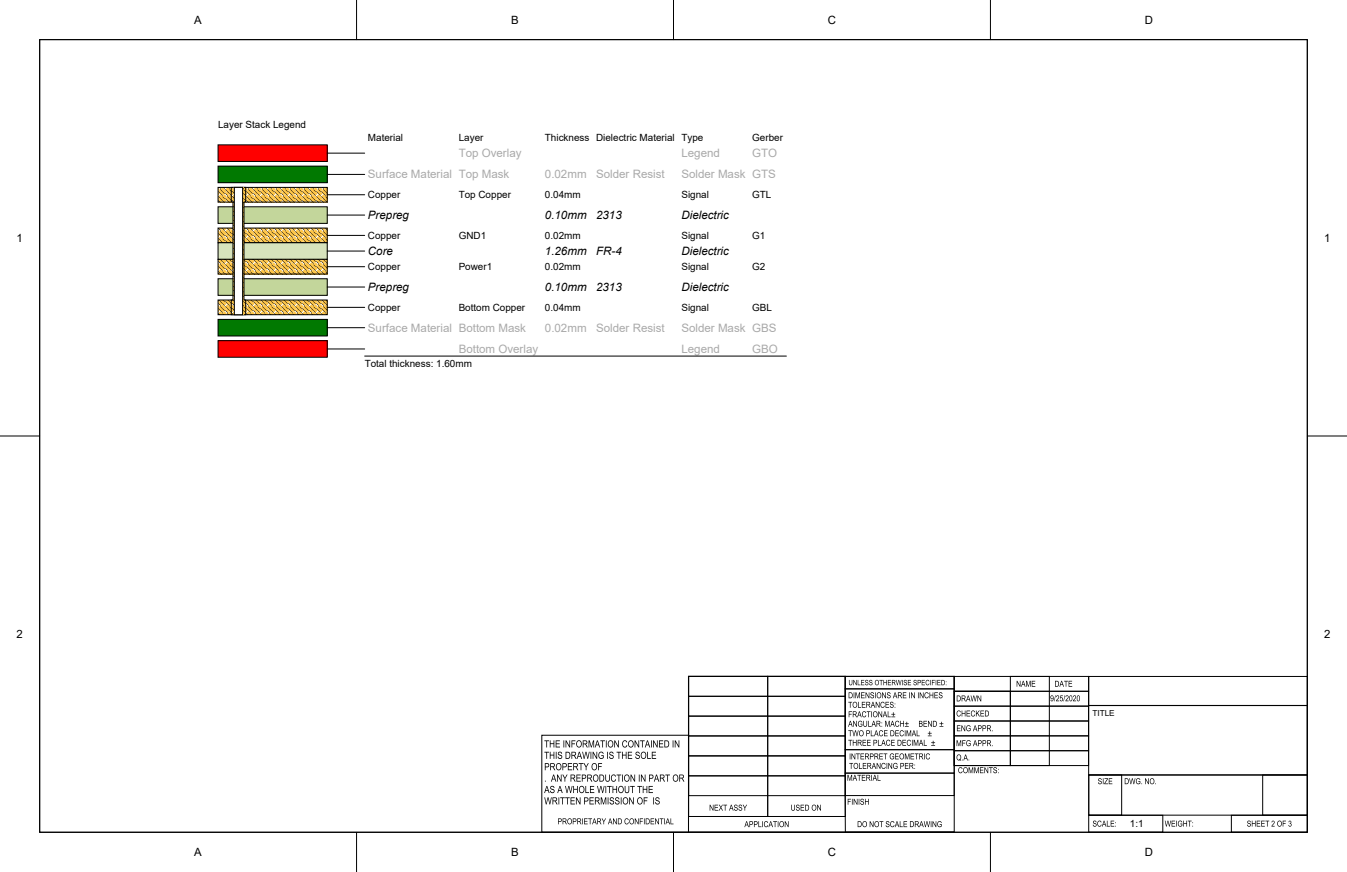
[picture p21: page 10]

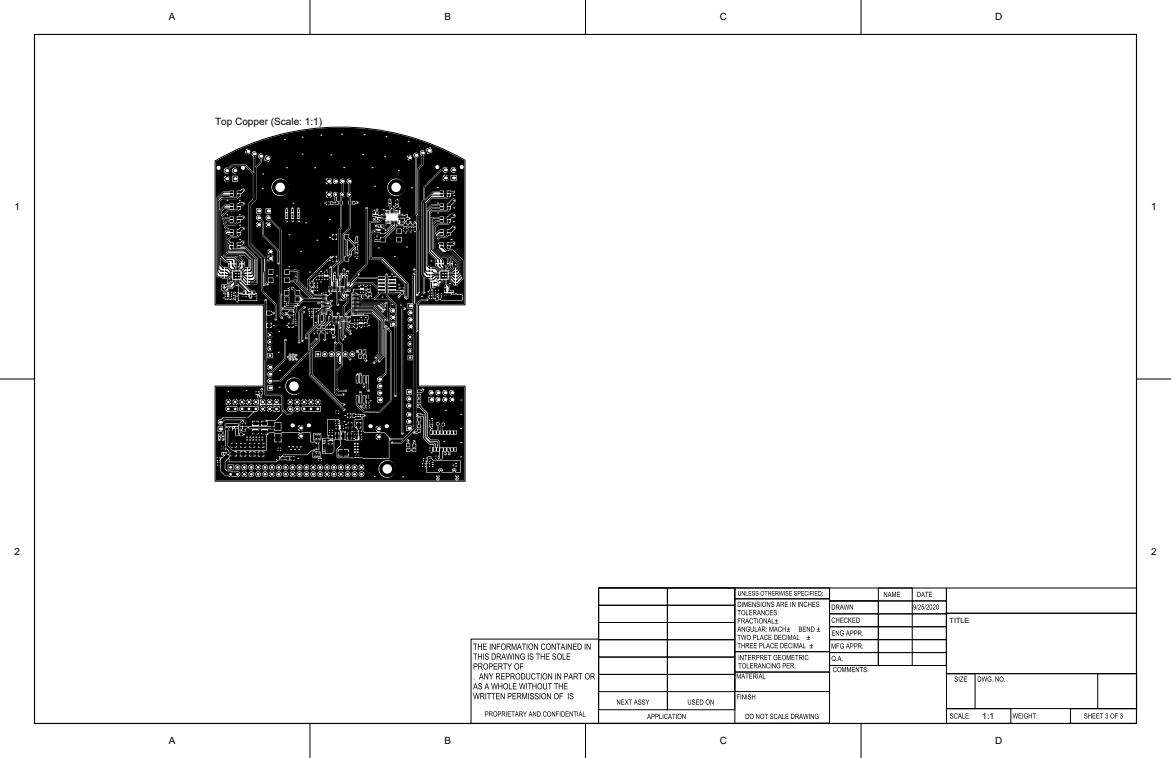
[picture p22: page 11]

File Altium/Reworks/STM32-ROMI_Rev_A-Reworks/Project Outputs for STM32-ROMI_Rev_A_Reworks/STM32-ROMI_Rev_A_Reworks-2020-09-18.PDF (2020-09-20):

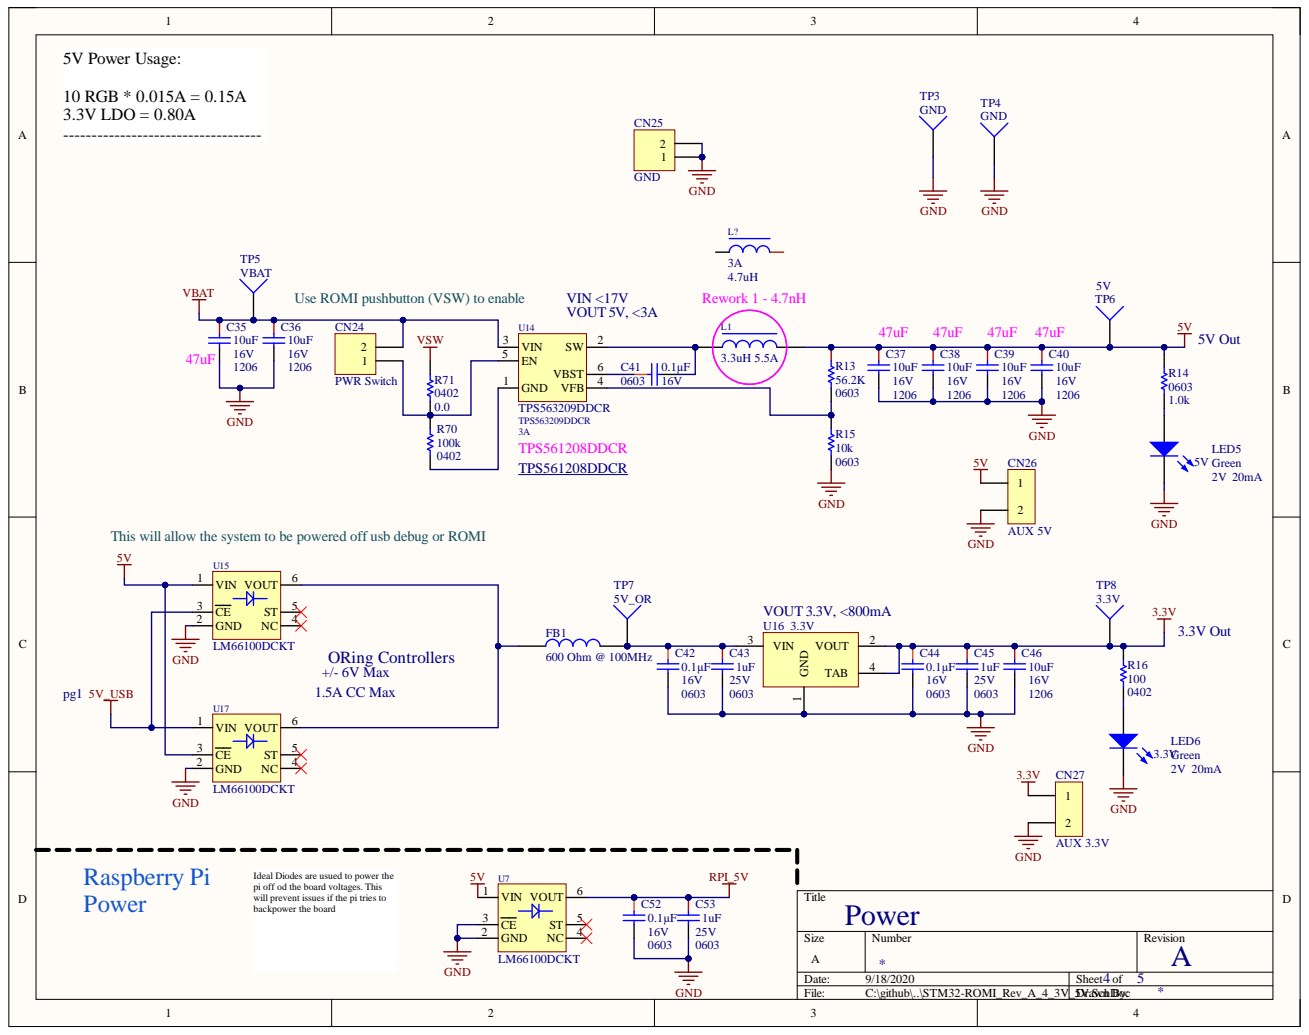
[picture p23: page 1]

Use ROMI pushbutton (VSW) to enable

This will allow the system to be powered off usb debug or ROMI

Ideal Diodes are usued to power the
pi off od the board voltages. This
will prevent issues if the pi tries to
backpower the board


IMU I/O Titl e | Altium L i mite d L3, 12a Rodborough Rd Frenchs Forest NSW Austral ia 20 86

A4 S i z e : | 9 1 5 2 0 2 0 Numbe r : | A R e vision:

Date : 9/18/202 0 Time : 3:17:33 P M | | She e t 5 of 6


Title | Altium Limited L3, 12a Rodborough Rd Frenchs Forest NSW Australia 2086

A4 Size: | Number: | Revision:

Date: 9/18/2020 Time: 3:17:33 PM | | Sheet of

C:\github\STM32-ROMI\Altium\Reworks\STM32-ROMI_Rev_A-Reworks\STM32-ROMI_Rev_A_0_Title.SchDoc


TCK/SWDCLK | PA14(JTCK-SWCLK) 49 | ROMI_SLPR

SPI_CS_AUX pg5 pg2 pg2 pg2 pg2 pg2 | PA15 50 | SERVO1_PWM

0.0 | | REV_B1

0.0 | REV_B2

C:\github\STM32-ROMI\Altium\Reworks\STM32-ROMI_Rev_A-Reworks\STM32-ROMI_Rev_A_1_STM32.SchDoc


URXD: connect to TX of microcontroller
UTXD: connect to RX of microcontroller
GPIO0: connect to RESET of microcontroller
GPIO2: optionally connect green LED to 3.3V (indicates wifi status)

Title | Altium Limited L3, 12a Rodborough Rd Frenchs Forest NSW Australia 2086

A4 Size: | Number: | Revision:

Date: 9/18/2020 Time: 3:17:34 PM | | Sheet of

C:\github\STM32-ROMI\Altium\Reworks\STM32-ROMI_Rev_A-Reworks\STM32-ROMI_Rev_A_2_Connectors.SchDoc



Rework 1 - 3.3uH changed to 4.7uH
Rework 2 - 5V buck is wrong version
Rework 3 - CN20 silk flipped

Title | Altium Limited L3, 12a Rodborough Rd Frenchs Forest NSW Australia 2086

A4 Size: | Number: | Revision:

Date: 9/18/2020 Time: 3:17:34 PM | | Sheet of

C:\github\STM32-ROMI\Altium\Reworks\STM32-ROMI_Rev_A-Reworks\STM32-ROMI_Rev_A_6_Reworks.SchDoc


View from Top side (Scale 1:1)



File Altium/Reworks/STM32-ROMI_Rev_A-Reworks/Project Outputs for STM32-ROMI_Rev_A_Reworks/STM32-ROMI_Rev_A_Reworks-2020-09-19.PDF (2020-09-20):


Use ROMI pushbutton (VSW) to enable

This will allow the system to be powered off usb debug or ROMI

Ideal Diodes are usued to power the
pi off od the board voltages. This
will prevent issues if the pi tries to
backpower the board


IMU I/O Titl e | Altium L i mite d L3, 12a Rodborough Rd Frenchs Forest NSW Austral ia 20 86

A4 S i z e : | 9 1 5 2 0 2 0 Numbe r : | A R e vision:

Date : 9/19/202 0 Time : 2:28:15 P M | | She e t 5 of 6


Title | Altium Limited L3, 12a Rodborough Rd Frenchs Forest NSW Australia 2086

A4 Size: | Number: | Revision:

Date: 9/19/2020 Time: 2:28:16 PM | | Sheet of

C:\github\STM32-ROMI\Altium\Reworks\STM32-ROMI_Rev_A-Reworks\STM32-ROMI_Rev_A_0_Title.SchDoc


TCK/SWDCLK | PA14(JTCK-SWCLK) 49 | ROMI_SLPR

SPI_CS_AUX pg5 pg2 pg2 pg2 pg2 pg2 | PA15 50 | SERVO1_PWM

0.0 | | REV_B1

0.0 | REV_B2

C:\github\STM32-ROMI\Altium\Reworks\STM32-ROMI_Rev_A-Reworks\STM32-ROMI_Rev_A_1_STM32.SchDoc


URXD: connect to TX of microcontroller
UTXD: connect to RX of microcontroller
GPIO0: connect to RESET of microcontroller
GPIO2: optionally connect green LED to 3.3V (indicates wifi status)

Title | Altium Limited L3, 12a Rodborough Rd Frenchs Forest NSW Australia 2086

A4 Size: | Number: | Revision:

Date: 9/19/2020 Time: 2:28:16 PM | | Sheet of

C:\github\STM32-ROMI\Altium\Reworks\STM32-ROMI_Rev_A-Reworks\STM32-ROMI_Rev_A_2_Connectors.SchDoc



Title | Altium Limited L3, 12a Rodborough Rd Frenchs Forest NSW Australia 2086

A4 Size: | Number: | Revision:

Date: 9/19/2020 Time: 2:28:16 PM | | Sheet of

C:\github\STM32-ROMI\Altium\Reworks\STM32-ROMI_Rev_A-Reworks\STM32-ROMI_Rev_A_6_Notes.SchDoc


Rework 1 - 3.3uH changed to 4.7uH
Rework 2 - 5V buck is wrong version
Rework 3 - CN20 silk flipped

Title | Altium Limited L3, 12a Rodborough Rd Frenchs Forest NSW Australia 2086

A4 Size: | Number: | Revision:

Date: 9/19/2020 Time: 2:28:16 PM | | Sheet of

C:\github\STM32-ROMI\Altium\Reworks\STM32-ROMI_Rev_A-Reworks\STM32-ROMI_Rev_A_7_Reworks.SchDoc


View from Top side (Scale 1:1)



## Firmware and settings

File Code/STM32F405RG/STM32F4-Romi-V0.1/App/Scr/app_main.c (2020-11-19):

/** ****************************************************************************
//
//  @file  app_main.cpp
//
//  Project:  STM32-Romi.
//
//  @brief   handle main application loop
//
//  Created: Kyle Rodrigues
//
//Change Notes:
 * 8/29/2020
 * added Sonar left and right
 * added header and main files for oled screen
 * esp link http://192.168.4.1 | 	192.168.50.85
 *
 * To Do:
 * Work on PID Loop
 * Confirm PWM channel timer is 16bit or 32 bit
 * confirm PID Period and Duty is correct
 *
// remove all uneccessary code to check speed and see if delays are errors
// *****************************************************************************
*/
/* Includes ------------------------------------------------------------------*/
#include <string.h>
#include <stdio.h>
#include <stdbool.h> //this is required to use bool statements
#include "math.h"
#include "main.h"
#include "can.h"
#include "dac.h"
#include "i2c.h"
#include "spi.h"
#include "tim.h"
#include "usart.h"
#include "gpio.h"
#include "stm32f4xx_it.h"
#include "stm32f4xx_hal.h"
#include "stm32f4xx_hal_tim.h"
#include "stm32f4xx_hal_tim_ex.h"


//******Custom Files******

#include "app_main.h"
#include "motors.h"
#include "control.h"
#include "edge_sensor.h"
#include "PID.h"
#include "encoder.h"
#include "interupt.h" // Sonar
#include "sonar.h"
#include "ui.h"


//OLED Includes
#include "fonts.h"
#include "ssd1306.h"
#include "test.h"
#include "bitmap.h"

//******timers******
extern TIM_HandleTypeDef htim2;
extern TIM_HandleTypeDef htim3;
extern TIM_HandleTypeDef htim4;
extern TIM_HandleTypeDef htim5;
extern TIM_HandleTypeDef htim9; //sonar 1uSec

SONAR_STATUS SONARS[] ={{"Left",TRIGL_GPIO_Port,TRIGL_Pin,ECHOL_GPIO_Port,ECHOL_Pin,0,0.0},
						{"Right",TRIGR_GPIO_Port,TRIGR_Pin,ECHOR_GPIO_Port,ECHOR_Pin,0,0.0},
						{"Center",TRIG_CTR_GPIO_Port,TRIG_CTR_Pin,ECHO_CTR_GPIO_Port,ECHO_CTR_Pin,0,0.0}};


//Sonar ticks set to zero
uint32_t numTicks = 0;

#define LED_BLINK_RATE 50 //50*10mS = 1/2 sec

char updatescr[10]; //use to update screen


//PID
#define KP 0.035f
#define KI 1.0f

//#define KP 0.065
//#define KI 2.0

#define TICK_RATE 10 //10mS
#define PID_RATE  2 //2*10mS

#define DT ((float)(TICK_RATE*PID_RATE)/1000)

// declare the PID state variables
PID pid_right = {KP,KI,DT,false,"Right", {0.0f,0.0f,0.0f,0.0f,0.0f}};
PID pid_left  = {KP,KI,DT,false,"Left", {0.0f,0.0f,0.0f,0.0f,0.0f}};

//PID pid_right = {KP,KI,DT,true,"Right", {0.0f,0.0f,0.0f,0.0f,0.0f}};
//PID pid_left  = {KP,KI,DT,true,"Left", {0.0f,0.0f,0.0f,0.0f,0.0f}};


ENC_STATUS enc_right = {0,0,0,"Right", 0, &htim3,{0.0f,0.0f}};
ENC_STATUS enc_left = {0,0,0,"Left", 0, &htim5,{0.0f,0.0f}};



// Hardware Revision bits
uint8_t RevBit[3];


// main application loop
void appMain(void){


	/* Check Hardware Revision Bits*/
	RevBit[0] =	HAL_GPIO_ReadPin(REV_BIT0_GPIO_Port, REV_BIT0_Pin);
	RevBit[1] =	HAL_GPIO_ReadPin(REV_BIT1_GPIO_Port, REV_BIT1_Pin);
	RevBit[2] =	HAL_GPIO_ReadPin(REV_BIT2_GPIO_Port, REV_BIT2_Pin);

	//Start the 1uSec timer for sonar
	HAL_TIM_Base_Start(&htim9);

	//hal pwm start
	HAL_TIM_PWM_Start(&htim2, TIM_CHANNEL_3);  //Start PWM
	HAL_TIM_PWM_Start(&htim4, TIM_CHANNEL_1);  //Start PWM

	//hal encoder start
	HAL_TIM_Encoder_Start(&htim3, TIM_CHANNEL_ALL);
	HAL_TIM_Encoder_Start(&htim5, TIM_CHANNEL_ALL);

	uint32_t ledTimer=LED_BLINK_RATE;
	uint32_t PIDTimer = PID_RATE;

	printf("Power up initiated...\r\n");
	printf("All systems nominal..\r\n");
	printf("Hardware Revision: %d%d%d\r\n",RevBit[2],RevBit[2],RevBit[2]);

	//Initialize OLED
	SSD1306_Init();
	SSD1306_Clear();
	SSD1306_DrawBitmap(0, 0, ologic, 128, 64, 1);
	SSD1306_UpdateScreen();
	HAL_Delay(2000);
	SSD1306_Clear();
	//SSD1306_GotoXY(40, 20);
	//SSD1306_Puts("OWO", &Font_16x26, 1);
	//SSD1306_UpdateScreen();
	//HAL_Delay(2000);
	SSD1306_Clear();
	SSD1306_GotoXY(30, 0);
	SSD1306_Puts("STM32-ROMI", &Font_7x10, 1);
	SSD1306_GotoXY(0, 30);
	SSD1306_Puts("E", &Font_7x10, 1);
	SSD1306_GotoXY(0, 40);
	SSD1306_Puts("D", &Font_7x10, 1);
	SSD1306_GotoXY(0, 50);
	SSD1306_Puts("S", &Font_7x10, 1);
	SSD1306_UpdateScreen();


	uint32_t tick = HAL_GetTick();

	//Set Sleep bits to 1 for enable
	HAL_GPIO_WritePin(ROMI_SLPL_GPIO_Port, ROMI_SLPL_Pin, SET);
	HAL_GPIO_WritePin(ROMI_SLPR_GPIO_Port, ROMI_SLPR_Pin, SET);

	//Edge Sensors
	enableEdgeSensors(BUMP_BIT_LEFT | BUMP_BIT_RIGHT);

	//Main program to loop forever
	while(1){
		uint32_t tock = HAL_GetTick();

		bool pid_update=false;     // flag to say if we should update the PID this time through the loop
		bool send_telemetry=false; // flag to say if we should send updated telemetry data to host this time through the loop


		if(tock-tick>TICK_RATE){ // 10ms timer (this 'if' is true once every 10ms)

			ledTimer--; // blink LED at LED_BLINK_RATE
			if(ledTimer==0){
				ledTimer = LED_BLINK_RATE; //0.5 Sec blink
				HAL_GPIO_TogglePin(Blinky_GPIO_Port, Blinky_Pin);
			}

			PIDTimer --; // see if we should run the PID update this time through the loop
			if(PIDTimer==0) {
				PIDTimer=PID_RATE;
				pid_update=true; // flag to update PID this time
                send_telemetry=true; // also send new telemetry after we update the PID

                /*
				//set the motor drivers on
				HAL_GPIO_WritePin(ROMI_SLPL_GPIO_Port, ROMI_SLPL_Pin, SET);
				HAL_GPIO_WritePin(ROMI_SLPR_GPIO_Port, ROMI_SLPR_Pin, SET);
				*/

				//Check the sonars
				checkSonar(&SONARS[SONAR1]);
				checkSonar(&SONARS[SONAR2]);

			}
			tick = tock;

			//check Edge Sensors
			updateEdgeSensors();  //update the state of the edge sensors


		}

		// update the motor controller state (handles driving to distance/turns etc)
		// will also update the PID controller if the flag is set
		MotorEvent event = updateMotors(pid_update,DT); // returns events flags if state changed or edge sensor triggered etc

		if(pid_update) {
					setPIDState(&pid_left.state,&pid_right.state);
					setEncoderState(&enc_left.state,&enc_right.state);
		}


		/// use this to adjust the pwm

		int c = getchar();
			if(c != EOF){
				putchar(c);
				switch (c) {
					case 'w':
						drive(MAX_LIN_VEL/2.0f,0.0f);
						break;

					case 'd':
						setMotorSpeed(0.5f, 0.8f);
						break;

					case 'a':
						drive(0.0f,MAX_ANG_VEL/2.0f);
						break;

					case 's':
						drive(0.0f,-MAX_ANG_VEL/4.0f);
						break;

				/*	case 'o':  // put PID in closed loop mode
						setOpenLoop(&pid_left,false);
						setOpenLoop(&pid_right,false);
						//printf("Motors In Closed Loop Mode\n");
						break;

					case 'O':  // put PID in open loop mode
						setOpenLoop(&pid_left,true);
						setOpenLoop(&pid_right,true);
						//printf("Motors In Open Loop Mode\n");
						break;
				*/

					case '1': // return event to start controller in table top challenge level 1 mode
						 event |= CE_M1;
						break;

					case '2': // return event to start controller in table top challenge level 1 mode
						 event |= CE_M2;
						break;

					case ' ':
						STOP();
						break;
					default:
						break;
				}

				}else{
				clearerr(stdin); // Reset the EOF Condition
				}

			updateControler(event); // update the main state machine (giving it any events that should be handled)
			/*
			if(send_telemetry) { // if flag is set send new telemetry data to the host
				sendTelemetry();
			}*/

			} //end of while loop



} //end of main loop

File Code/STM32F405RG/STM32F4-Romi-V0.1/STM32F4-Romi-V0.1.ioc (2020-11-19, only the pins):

Mcu.UserName=STM32F405RGTx
PA0-WKUP.GPIO_Label=ENCL_CHA
PA0-WKUP.Signal=S_TIM5_CH1
PA1.GPIO_Label=ENCL_CHB
PA1.Signal=S_TIM5_CH2
PA10.GPIO_Label=TRIGR
PA10.Signal=GPIO_Output
PA11.Signal=CAN1_RX
PA12.Signal=CAN1_TX
PA13.Signal=SYS_JTMS-SWDIO
PA14.Signal=SYS_JTCK-SWCLK
PA15.GPIO_Label=SPI_CS_AUX
PA15.Signal=GPIO_Output
PA2.Signal=USART2_TX
PA3.Signal=USART2_RX
PA4.Signal=COMP_DAC1_group
PA5.GPIO_Label=Blinky
PA5.Signal=GPIO_Output
PA6.Signal=SPI1_MISO
PA7.Signal=SPI1_MOSI
PA8.Signal=I2C3_SCL
PA9.GPIO_Label=ECHOR
PA9.Signal=GPXTI9
PB0.GPIO_Label=TRIGL
PB0.Signal=GPIO_Output
PB1.GPIO_Label=ECHOL
PB1.Signal=GPXTI1
PB10.GPIO_Label=ROMI_PWMR
PB10.Signal=S_TIM2_CH3
PB12.GPIO_Label=QTRL
PB12.Signal=GPXTI12
PB13.GPIO_Label=ROMI_DIRR
PB13.Signal=GPIO_Output
PB14.GPIO_Label=ROMI_SLPR
PB14.Signal=GPIO_Output
PB15.GPIO_Label=SERVO1_PWM
PB15.Signal=S_TIM12_CH2
PB2.GPIO_Label=QTRR
PB2.Signal=GPXTI2
PB3.Signal=SPI1_SCK
PB4.GPIO_Label=ENCR_CHA
PB4.Signal=S_TIM3_CH1
PB5.GPIO_Label=ENCR_CHB
PB5.Signal=S_TIM3_CH2
PB6.GPIO_Label=ROMI_PWML
PB6.Signal=S_TIM4_CH1
PB7.Signal=I2C1_SDA
PB8.Signal=I2C1_SCL
PB9.GPIO_Label=SERVO2_PWM
PB9.Signal=S_TIM11_CH1
PC0.GPIO_Label=IMU_RST
PC0.Signal=GPIO_Output
PC1.GPIO_Label=REV_BIT0
PC1.Signal=GPIO_Output
PC10.Signal=USART3_TX
PC11.Signal=USART3_RX
PC12.GPIO_Label=ROMI_DIRL 
PC12.Signal=GPIO_Output
PC13-ANTI_TAMP.GPIO_Label=OLED_BTN
PC13-ANTI_TAMP.Signal=GPXTI13
PC14-OSC32_IN.Signal=RCC_OSC32_IN
PC15-OSC32_OUT.Signal=RCC_OSC32_OUT
PC2.GPIO_Label=REV_BIT1
PC2.Signal=GPIO_Input
PC3.GPIO_Label=REV_BIT2
PC3.Signal=GPIO_Input
PC4.GPIO_Label=RGB_INT1
PC4.Signal=GPIO_Output
PC5.GPIO_Label=RGB_INT2
PC5.Signal=GPIO_Output
PC6.GPIO_Label=ROMI_SLPL
PC6.Signal=GPIO_Output
PC7.GPIO_Label=ECHO_CTR
PC7.Signal=GPXTI7
PC8.GPIO_Label=TRIG_CTR
PC8.Signal=GPIO_Output
PC9.Signal=I2C3_SDA
PD2.GPIO_Label=SPI_CS_FLASH
PD2.Signal=GPIO_Output
PH0-OSC_IN.Signal=RCC_OSC_IN
PH1-OSC_OUT.Signal=RCC_OSC_OUT

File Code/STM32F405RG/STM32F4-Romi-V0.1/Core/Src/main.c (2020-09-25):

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
/* Includes ------------------------------------------------------------------*/
#include "main.h"
#include "can.h"
#include "dac.h"
#include "i2c.h"
#include "spi.h"
#include "tim.h"
#include "usart.h"
#include "gpio.h"

/* USER CODE BEGIN Includes */
#include <stdio.h>
#include <string.h>
#include <stm32f4xx_hal.h>
#include "app_main.h"

//******Setup PrintF****
#define IO_UART huart2 // **** change this to the UART your board uses ****

/* USER CODE END Includes */

/* USER CODE BEGIN PTD */
//void TIM6_DAC_IRQHandler(void);
//void HAL_TIM_PeriodElapsedCallback(TIM_HandleTypeDef *htim6);

/* USER CODE END PTD */

/* USER CODE BEGIN PD */
//extern the timer variable to pass it to the interrupt
extern TIM_HandleTypeDef htim2;
extern TIM_HandleTypeDef htim3;
extern TIM_HandleTypeDef htim4;
extern TIM_HandleTypeDef htim5;
extern TIM_HandleTypeDef htim9; //Sonar 1mS Timer
extern UART_HandleTypeDef huart2;

/* USER CODE END PD */


void SystemClock_Config(void);
/* USER CODE BEGIN PFP */

void TIM6_DAC_IRQHandler(void);
void HAL_TIM_PeriodElapsedCallback(TIM_HandleTypeDef *htim6);
void HAL_TIM_PeriodElapsedCallback(TIM_HandleTypeDef *htim9);
/* USER CODE END PFP */

/**
  * @brief  The application entry point.
  * @retval int
  */
int main(void)
{
  /* MCU Configuration--------------------------------------------------------*/

  /* Reset of all peripherals, Initializes the Flash interface and the Systick. */
  HAL_Init();

  /* Configure the system clock */
  SystemClock_Config();

  /* Initialize all configured peripherals */
  MX_GPIO_Init();
  MX_TIM2_Init();
  MX_TIM3_Init();
  MX_USART2_UART_Init();
  MX_DAC_Init();
  MX_I2C1_Init();
  MX_I2C3_Init();
  MX_SPI1_Init();
  MX_TIM4_Init();
  MX_TIM5_Init();
  MX_TIM6_Init();
  MX_TIM9_Init();
  MX_TIM12_Init();
  MX_TIM11_Init();
  MX_USART3_UART_Init();
  MX_CAN1_Init();
  /* USER CODE BEGIN 2 */
  //Start the timer
  HAL_TIM_Base_Start_IT(&htim6);


  /* USER CODE END 2 */

  /* Infinite loop */
  /* USER CODE BEGIN WHILE */
  while (1)
  {

	  appMain(); // will not return from here
    /* USER CODE END WHILE */

    /* USER CODE BEGIN 3 */
  }
  /* USER CODE END 3 */
}

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
/* USER CODE BEGIN 4 */

/* This function sets up the serial printf*/
int __io_putchar(int ch) {
    HAL_StatusTypeDef sts = HAL_UART_Transmit(&IO_UART ,(uint8_t*)&ch,1,10);
    if(sts == HAL_OK) {
        return ch;
    }
    return EOF;
}
int __io_getchar(void) {
    if(__HAL_UART_GET_FLAG(&IO_UART , UART_FLAG_RXNE)) {
        uint8_t ch=0;
        __HAL_UART_CLEAR_FEFLAG(&IO_UART );
        __HAL_UART_CLEAR_OREFLAG(&IO_UART );
        __HAL_UART_CLEAR_PEFLAG(&IO_UART );
        HAL_StatusTypeDef sts = HAL_UART_Receive(&IO_UART ,&ch,1,1);
        if(sts == HAL_OK) {
            return (int)ch;
        }
    }
    return EOF;
}
int _read(int file, char *ptr, int len){
int DataIdx;
    for (DataIdx = 0; DataIdx < len; DataIdx++) {
        int ch =  __io_getchar();
        if(ch != EOF) {
             *ptr++ = ch;
        }
        else {
            return DataIdx;
        }
    }
    return len;
}

/* USER CODE END 4 */
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


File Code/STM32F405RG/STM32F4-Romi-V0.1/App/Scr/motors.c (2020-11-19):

/*
 * motors.c
 *
 *  Created on: Sep 11, 2020
 *      Author: Kyle Rodrigues
 *
 *     | DIR | PWM | /SLEEP | MOTOR+ | MOTOR- |OPERATION
 *     |  0  | PWM |    1   |  PWM   |   L    | Forward/break at speed of %PWM
 *     |  1  | PWM |    1   |   L    |  PWM   | Reverse/break at speed of %PWM
 *     |  X  |  0  |    1   |   L    |   L    |brake low - output shorted to gnd
 *     |  X  |  X  |    0   |   Z    |   Z    |Coast (outputs floating
 *
 *TIM2 = PWMR
 *TIM4 = PWML
 *
 *PWM Frequency 250kHZ
 *
 *encoder count 1440
 *gear ratio 120:1
 *Max RPM 150, PRS =
 *
 */

//Includes
#include <stdio.h>
#include "motors.h"
#include "main.h"
#include "app_main.h"
#include "PID.h"
#include "encoder.h"
#include "sonar.h"
#include "edge_sensor.h"

//// define robot geometry to calculate kinematics
#define WHEEL_BASE   0.087f // robot wheel base (distance between the wheels) m
#define WHEEL_RADIUS (0.070f/2.0f) // radius of the wheels (m)

// define PI and 2*PI as floats
const float M_PI_F = (3.141592653589793f);
const float M_2PI_F = (2.0f*3.141592653589793f);

// local prototypes
static void setMTRSpeed(float speed, const MOTOR_CONF *motor);
static void updatePose(float DT);

static float speed_l=0.0f; // desired left wheel speed (rad/sec)
static float speed_r=0.0f; // desired right wheel speed (rad/sec)

static float target_dist_2=0.0f;  // how far to drive (squared) when running a driveTo command - in meters
static float target_heading=0.0f; // how far to turn when running a turnTo command - in rad

// reference starting pose of robot when beginning a turnTo or driveTo command
static float start_pose_x=0.0f;
static float start_pose_y=0.0f;
static float start_heading=0.0f;

// current robot pose
float pose_x=0.0f;
float pose_y=0.0f;
float heading=0.0f;

// flags to control the driveTo and turnTo commands
static bool driving=false; // true if currently performing a driveTo or turnTo command
static bool turn_ccw=false; // set direction of turn in a turnTo, true = counter clock wise (to the left)

const MOTOR_CONF mot_left = {"Left",TIM_CHANNEL_1, &htim4, ROMI_DIRL_GPIO_Port, ROMI_DIRL_Pin}; //add a status bit?
const MOTOR_CONF mot_right = {"Right",TIM_CHANNEL_3, &htim2, ROMI_DIRR_GPIO_Port, ROMI_DIRR_Pin};

// Set PWM output for a motor for desired power
void setMTRSpeed(float speed, const MOTOR_CONF *motor){
	HAL_GPIO_WritePin(ROMI_SLPL_GPIO_Port, ROMI_SLPL_Pin, SET);
	HAL_GPIO_WritePin(ROMI_SLPR_GPIO_Port, ROMI_SLPR_Pin, SET);

	uint32_t direction = speed > 0?0:1; //if assignment, ternary operator
	speed = fabsf(speed); //takes speed and returns absolute value
	HAL_GPIO_WritePin(motor->gpio_port, motor->gpio_pin, direction==1 ?SET:RESET);

	if(speed > MOTOR_PWM_PERIOD){
		speed = MOTOR_PWM_PERIOD;
	}
	__HAL_TIM_SET_COMPARE(motor->htim,motor->tim_ch,(uint32_t)speed); //sets capture/compare register for the the duty; how fast the
}

// set target velocity for each wheel (in rad/s)
void setMotorSpeed(float left, float right) {
	speed_l = left;
	speed_r = right;
}
// set target velocities for each wheel based on desired robot dynamics
// lin_vel : desired linear velocity of robot center (m/s)
// ang_vel : desired angular velocity of robot (rad/s)
void drive(float lin_vel, float ang_vel) {
	speed_l =  (lin_vel - ang_vel * WHEEL_BASE/2.0f)/WHEEL_RADIUS;
	speed_r =  (lin_vel + ang_vel * WHEEL_BASE/2.0f)/WHEEL_RADIUS;
}

// stop both motors and cancel any driveTo or turnTo command that is executing
void STOP(void){
	printf("Stop Detected\n\r");
	speed_l = 0.0;
	speed_r = 0.0;
	setMTRSpeed(0.0f,&mot_right);
	setMTRSpeed(0.0f,&mot_left);
	//HAL_GPIO_WritePin(ROMI_SLPL_GPIO_Port, ROMI_SLPL_Pin, RESET);
	//HAL_GPIO_WritePin(ROMI_SLPR_GPIO_Port, ROMI_SLPR_Pin, RESET);

	// Cancel driving commands
	driving = false;
}

// update the motor controller and robot driving status
// if pid_update is true will update the PID controller also (and associated state like the encoders and output the speeds to the wheels)
// also updates the internal robot pose
// DT is the update period (sec) used for the inverse kinematics to update the internal pose estimate
//
// Returns any events that are triggered like end of driveTo or turnTo command or is a bump sensor is detected
//
// If at any time the motors are driving and an enabled bumb sensor detects a hit both motors are immediately stopped.
MotorEvent updateMotors(bool pid_update, float DT) {

	MotorEvent event = ME_NONE;

	if(pid_update) {// see if we should update the PID this time through
		float duty_l=0.0f; // left wheel output duty cycle  (-1.0 -- 1.0)
		float duty_r=0.0f; // right wheel output duty cycle (-1.0 -- 1.0)

		// get latest speed and position estimates from encoders
		updateEncoder(&enc_right);
		updateEncoder(&enc_left);

		// run PID for speed control
		duty_l = PID_update(speed_l,enc_left.vel,&pid_left);
		duty_r = PID_update(speed_r,enc_right.vel,&pid_right);


		// set output PWM duty for both motors
		setMTRSpeed(duty_r*MOTOR_PWM_PERIOD,&mot_right);
		setMTRSpeed(duty_l*MOTOR_PWM_PERIOD,&mot_left);

		updatePose(DT); // calculate updated pose

		// now test if we have completed a turn to or driveTo command (if one is running)
		float ref_heading = heading; // get current heading

		if(driving && (target_heading != 0.0f)) {  // if doing a turnTo command

			  // see if we will turn through 0 heading and handle wrap around of angles if needed
			if (((ref_heading < 0.0f) && (start_heading >=0.0f)) || ((ref_heading >= 0.0f) && (start_heading < 0.0f))) {

				// handle wrapping around target from + to - angles
				if(ref_heading < 0.0f ) {
					if(turn_ccw) {
					   ref_heading += M_2PI_F;
					}
				}
				else {
					if(!turn_ccw) {
					   ref_heading -= M_2PI_F;
					}
				}
			}

			// now see if we have turned far enough
			if(fabsf(ref_heading-start_heading) >= target_heading) {
				STOP();
				event = ME_DONE_TURN;
			}
		}

		// check if doing a driveTo command and stop if we have gone far enough
		if(driving && (target_dist_2 != 0.0f)) {

			// calculate squared magnitude of distance we have moved
			float dx=pose_x-start_pose_x;
			float dy=pose_y-start_pose_y;

			if (( dx*dx+dy*dy) >= target_dist_2) { // compare to square magnatude of target distance
				STOP(); // got htere so stop
				event = ME_DONE_DRIVE; // return done event
			}
		}

		if(driving) {
			//printf("sh=%5.2f, th=%5.2f, h=%5.2f, rh=%5.2f\n",start_heading,target_heading,heading,ref_heading);
		}

	}
	// check if either bumper has a hit (if enabled)
	bool leftClif = getEdgeSensorState(BUMP_BIT_LEFT)==ES_HIT;
	bool rightClif = getEdgeSensorState(BUMP_BIT_RIGHT)==ES_HIT;

	if(leftClif || rightClif) {
		STOP(); // stop if bumper hit
		event = leftClif?ME_BUMP_LEFT:ME_BUMP_RIGHT; // return event that bumper is hit
	}

	return event;
}
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

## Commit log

2020-07-14 Moving the project to public
    STM32 based robot to work on a ROMI base
    [FPGA_ROMI_Board.PcbDoc, STM32-ROMI-Pin_List_Rev_A.xlsx, STM32-ROMI_Rev_A.PrjPcb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]
2020-07-15 placed remaining caps on pcb
    -added descriptions to connectors and nets
    -placed missing capacitors
    [STM32-ROMI_Rev_A_1_STM32.SchDoc]
2020-07-15 Added more pin descriptions to headers
2020-07-22 connected 5V and 3V rails, added aux power connectors
    added i2c traces
    [STM32-ROMI_Rev_A_2_Connectors.SchDoc, STM32-ROMI_Rev_A_3_OLED_Sensor.SchDoc, STM32-ROMI_Rev_A_4_3V_5V.SchDoc]
2020-07-24 ROUTED RGN LEDS AND GPIO IO
    [STM32-ROMI_Rev_A_5_IMU_IO.SchDoc]
2020-07-24 adding 5V power path
2020-07-25 routed sonar and uart
2020-07-25 routed most of the traces
    [STM32-ROMI_Rev_A_2_Connectors.SchDoc]
2020-07-29 traces finished routing
    [STM32-ROMI_Rev_A.PrjPcb]
2020-07-30 cleaning DRC Errors
    [STM32-ROMI_Rev_A.PrjPcb, STM32-ROMI_Rev_A_0_Title.SchDoc]
2020-08-05 added revision bits, ready for review
    [STM32-ROMI_Rev_A.PrjPcb, STM32-ROMI_Rev_A_1_STM32.SchDoc]
2020-08-19 cleaning bom for fab
    [JLCSMT_Sample_BOM1.xlsx, STM32-ROMI_Rev_A-2020-08-18-JLCPCB.xls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]
2020-08-22 updated readme file
    [STM32-ROMI_Rev_A-2020-08-18-JLCPCB.xls]
2020-08-27 sent to the fab
    [STM32-ROMI_Rev_A-2020-08-18-JLCPCB.xls, STM32-ROMI_Rev_A-2020-08-18.csv, STM32-ROMI_Rev_A-2020-08-25-JLCPCB.xlsx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]
2020-08-30 added sonar function
2020-08-30 fixed pcba name
2020-09-02 added motor diver datasheet
2020-09-02 added truth table
    [STM32-ROMI_Rev_A_2_Connectors.SchDoc]
2020-09-06 got the oled working
    [STM32-ROMI_Rev_A.PrjPcb, STM32-ROMI_Rev_A_4_3V_5V.SchDoc, STM32-ROMI_Rev_A_6_Reworks.SchDoc]
2020-09-07 upated sonar funtion
    [STM32-ROMI-Pin_List_Rev_A.xlsx]
2020-09-10 fixed App source folder structure
    [STM32-ROMI_Rev_A_4_3V_5V.SchDoc]
2020-09-11 added rework changes
    [FPGA_ROMI_Board.PcbDoc, JLCSMT_Sample_BOM1.xlsx, STM32-ROMI-Pin_List_Rev_A.xlsx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]
2020-09-14 PWM and encoder code working
    [STM32-ROMI_Rev_A.PrjPcb, STM32-ROMI_Rev_A_Reworks.PrjPcb]
2020-09-18 started PID loop tuning
    got motors spinning, looks like aPID loop issue
    [STM32F4-Romi-V0.1.ioc, app_main.c, main.h]
2020-09-18 Got the motors working to control over telnet
2020-09-20 adding esp-link instructions
    [STM32-ROMI_Rev_A_4_3V_5V.SchDoc, STM32-ROMI_Rev_A_6_Notes.SchDoc, STM32-ROMI_Rev_A_7_Reworks.SchDoc]
2020-09-22 updated driving
    [STM32-ROMI-Pin_List_Rev_A.xlsx, STM32-ROMI_Rev_A_Reworks.PrjPcb]
2020-10-02 added edge sensor code
    [STM32-ROMI-Pin_List_Rev_A.xlsx]
2020-10-08 code updated working on edge sensors
2020-10-15 working with ralph, slightly better
    [STM32-ROMI-Pin_List_Rev_A.xlsx]
2020-11-02 trying to debug pid loop
2020-11-10 updated PID speed
2020-11-15 latest code with errors, ned to debug with ralph
    [app_main.c, motors.c]
2020-11-16 issues with PID
    [STM32-ROMI-Pin_List_Rev_A-1.xlsx]
2020-11-17 Code Working!
    SetMTR and setMotor were mixed up causing issues
    [STM32-ROMI-Pin_List_Rev_A-1.xlsx]

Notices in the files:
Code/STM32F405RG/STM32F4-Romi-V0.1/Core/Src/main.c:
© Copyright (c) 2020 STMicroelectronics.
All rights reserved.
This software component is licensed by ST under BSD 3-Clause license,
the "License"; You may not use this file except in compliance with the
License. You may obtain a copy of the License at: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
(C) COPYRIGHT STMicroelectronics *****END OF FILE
